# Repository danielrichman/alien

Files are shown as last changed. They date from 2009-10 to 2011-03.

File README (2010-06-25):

This is the code repository for the ALIEN Project:
ALtitude Imaging Entering Near-space

This project consists of
  Daniel Richman <main@danielrichman.co.uk>
  Simrun Basuita <simrunbasuita@googlemail.com>
  Alex Breton 
although Alex Breton will not be contributing any code

More information is here:
  http://wiki.ukhas.org.uk/projects:alien
  http://alienproject.wordpress.com/

All the code contained within this subversion repository is licensed under
GPL version 3. Please see the COPYING file.

All the code is Copyright (c) 2009: Daniel Richman (and/or) Simrun Basuita
Please see individual files for more details.

There are also some schematics licensed under the 
Creative Commons Attribution-Non-Commercial-Share Alike 2.0 UK: 
  England & Wales license.
Typically these are in alien1/eagle and alien2/eagle, and are marked 
accordingly.

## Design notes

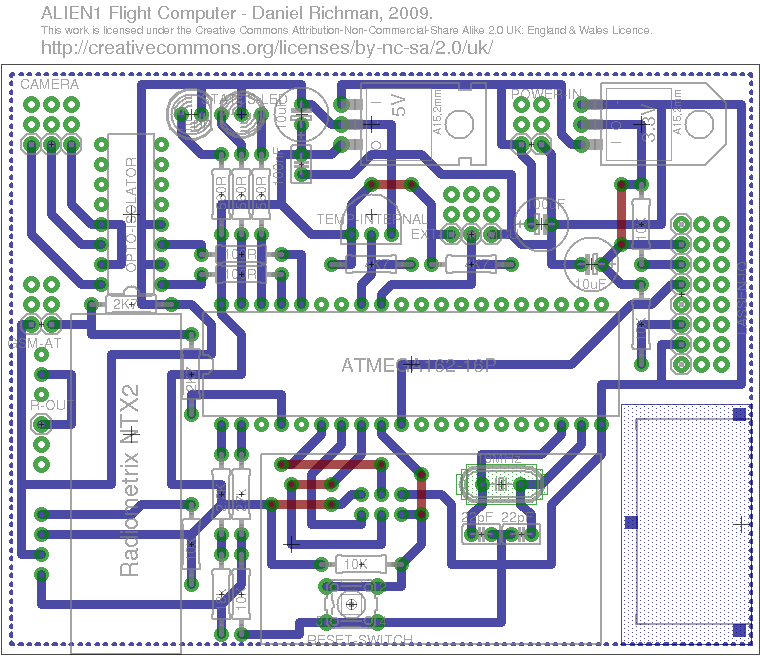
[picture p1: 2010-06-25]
alien1/eagle/alien1b.png

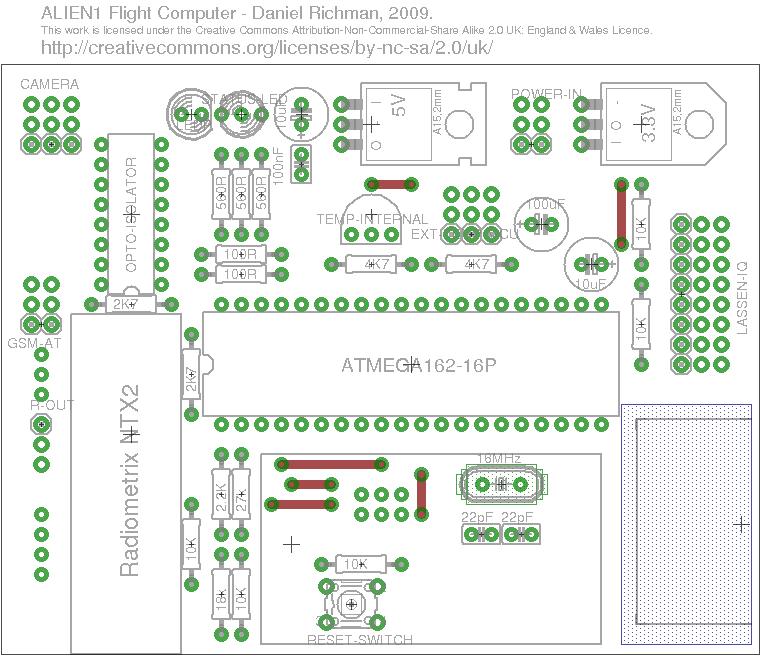
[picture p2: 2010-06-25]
alien1/eagle/alien1bn.png

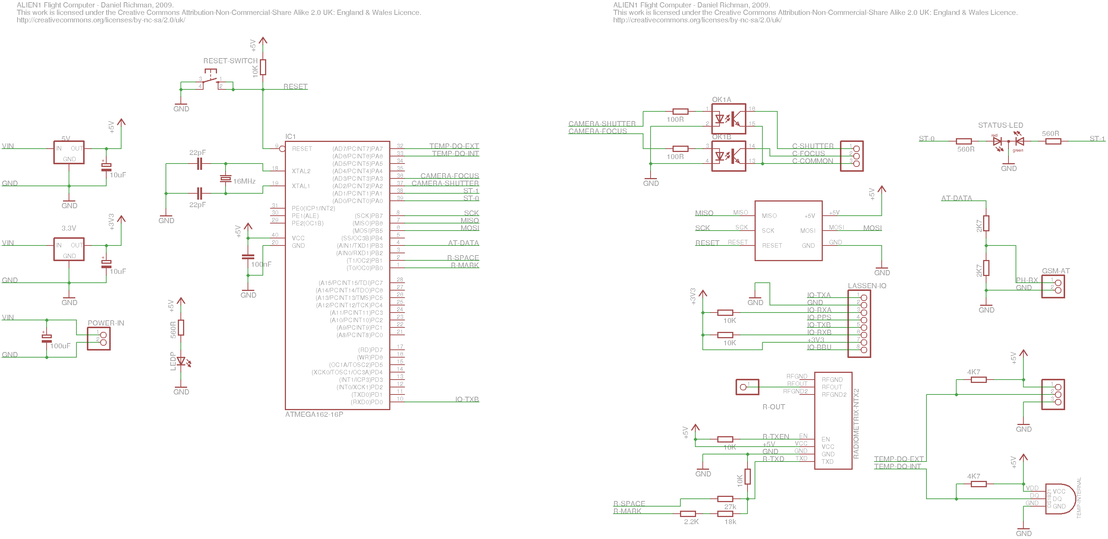
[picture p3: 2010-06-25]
alien1/eagle/alien1.png

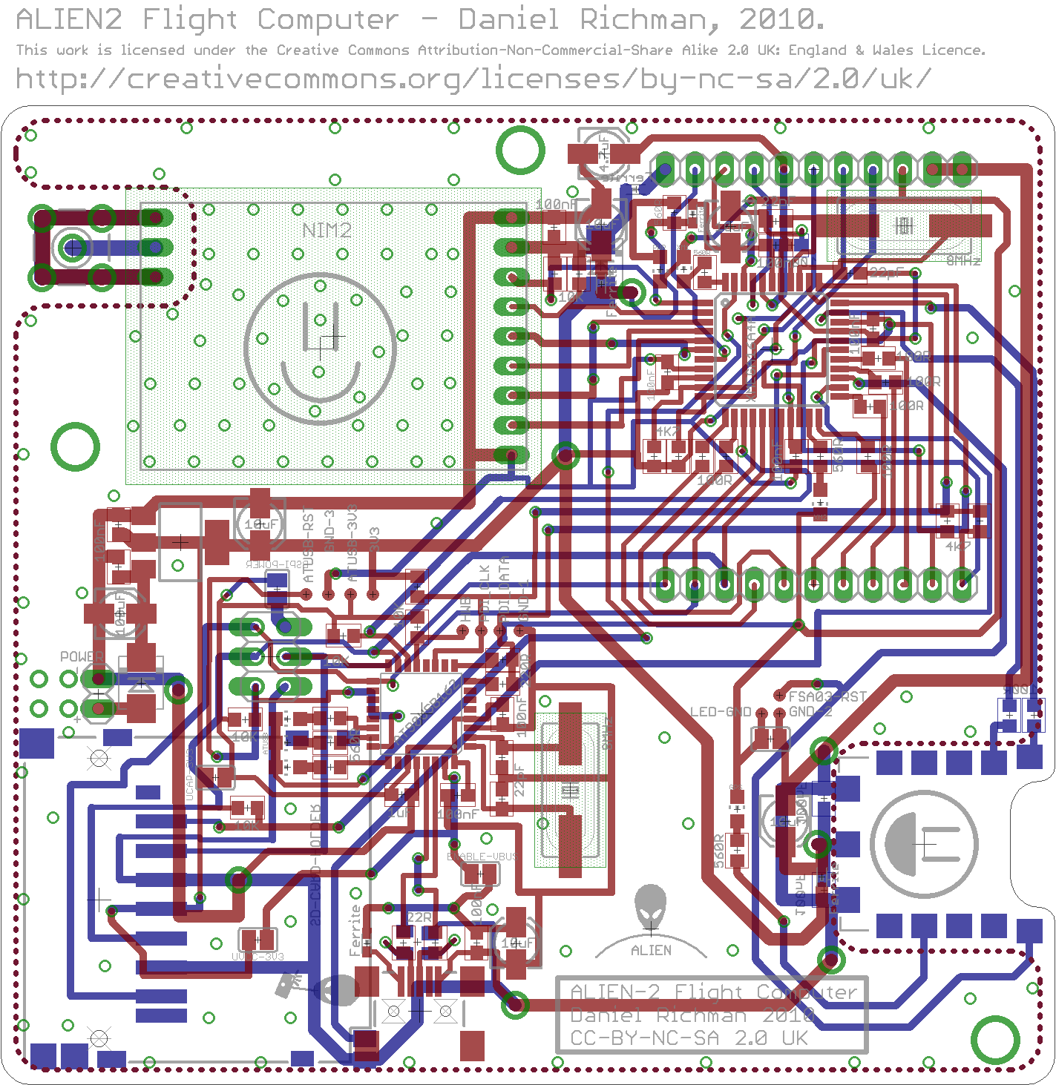
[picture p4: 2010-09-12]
alien2/eagle/alien2b.png

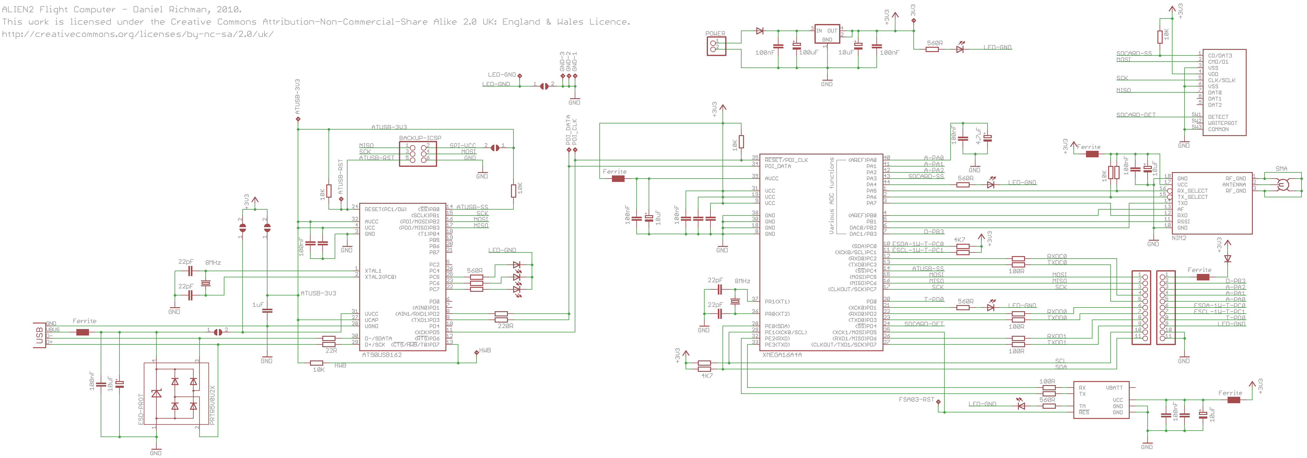
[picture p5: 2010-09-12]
alien2/eagle/alien2.png

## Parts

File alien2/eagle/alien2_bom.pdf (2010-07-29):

| Value | Device
2 | 22R | Resistor 0603 | 1500608
8 | 100R | Resistor 0603 | 1500583
2 | 220R | Resistor 0603 | 1500609
7 | 560R | Resistor 0603 | 1500642
4 | 4K7 | Resistor 0603 | 1500637
7 | 10K | Resistor 0603 | 1500585
4 | 22pF | Capacitor 0603 | 1414622
12 | 100nF | Capacitor 0603 | 1650834
1 | 1uF | Capacitor 0603 | 1650837
1 | 4.7uF | Electrolytic Capacitor 0405 | 1187021
5 | 10uF | Electrolytic Capacitor 0405 | 1469324
1 | 100uF | Electrolytic Capacitor 0603 | 8823065
2 | 8MHz | Crystal | 1611741
1 | | AT90USB162 | 1455073
5 | | Ferrite Bead 0603 | 1515756
3 | | Red LED 0805 | 1226392
2 | | Yellow LED 0805 | 1226420
2 | | Green LED 0805 | 1226373
1 | | PRTR5V0U2X | 1524157
1 | | SD Card Holder | 9186174
2 | | | 1651108
1 | | SMA | 1248989
1 | | TC2117-3.3V | 1605581
1 | | USB Connector | 1753806
1 | | XMEGA32A4 | 1748557
1 | | FSA03 | Already Have
1 | | NIM2 | Already Have
2 | | Pin Header 1x11
1 | | Pin Header 1X2
1 | | Pin Header 2x3
Qty | Farnell Order Code

Shottky Diode

Maplin
Maplin
Maplin

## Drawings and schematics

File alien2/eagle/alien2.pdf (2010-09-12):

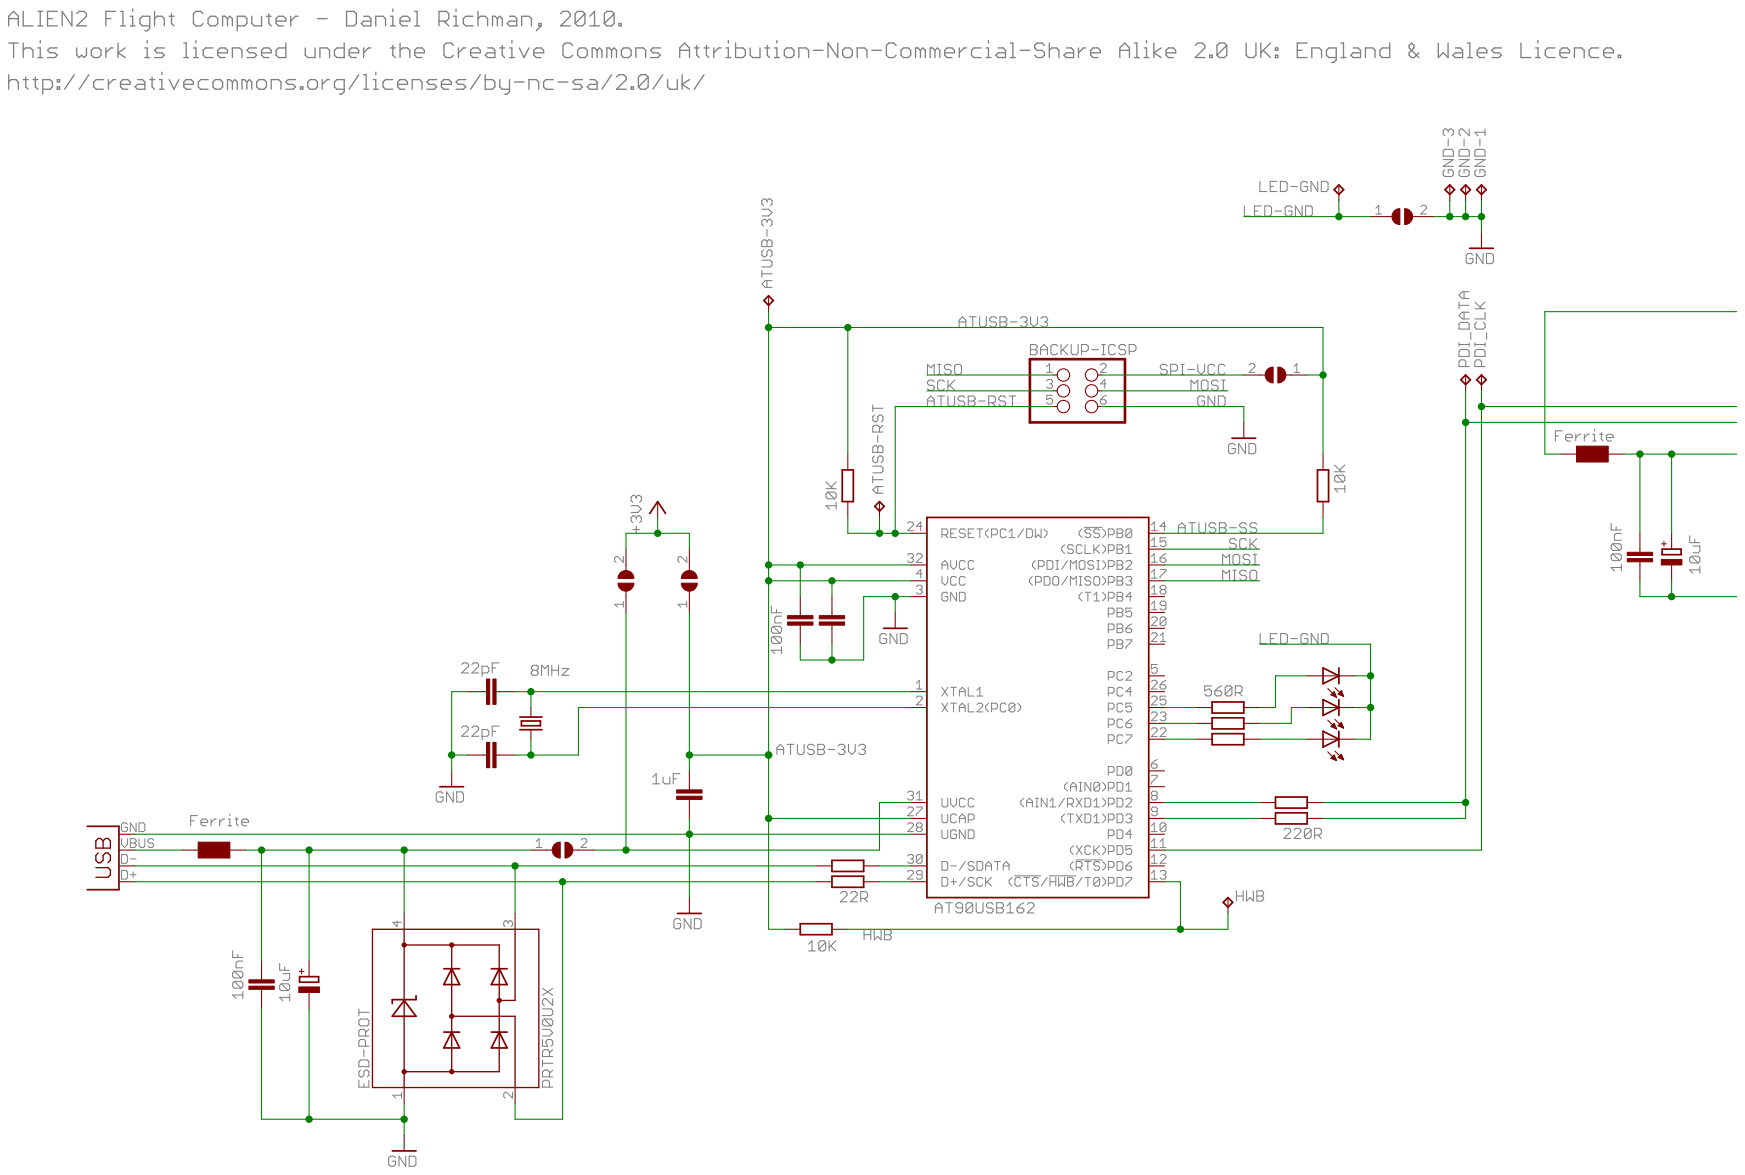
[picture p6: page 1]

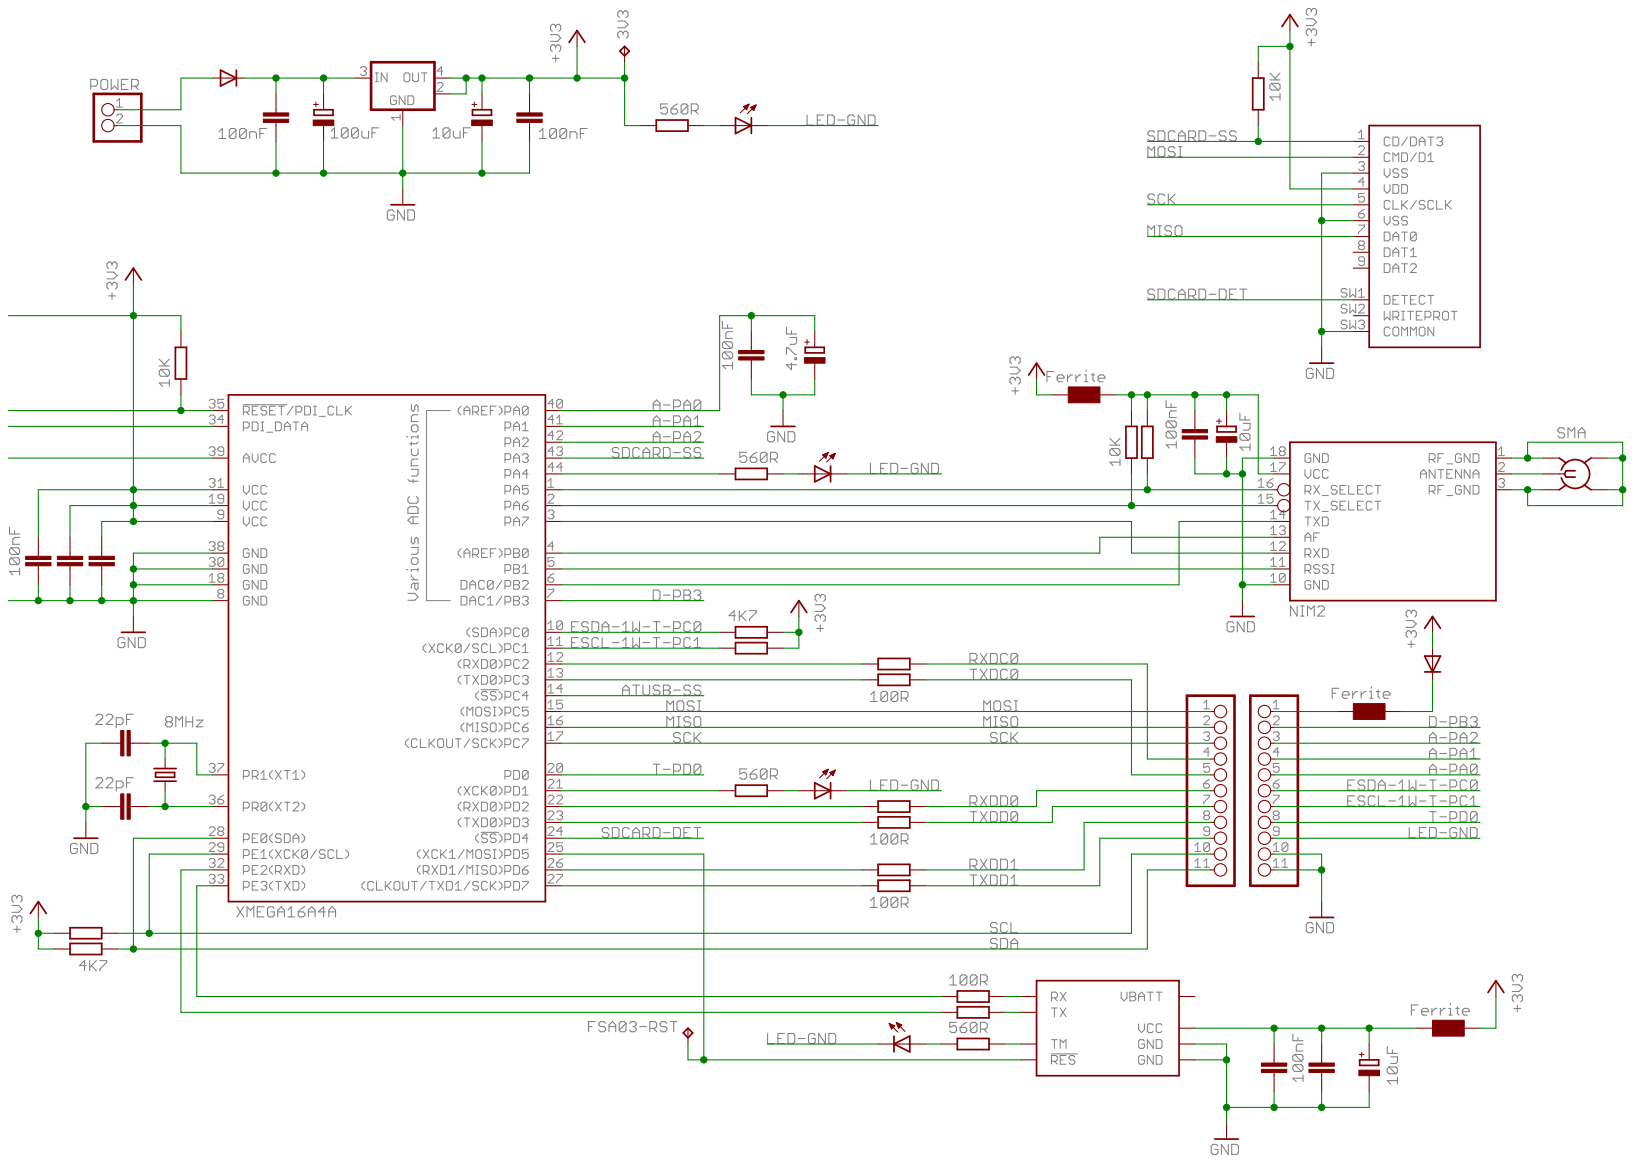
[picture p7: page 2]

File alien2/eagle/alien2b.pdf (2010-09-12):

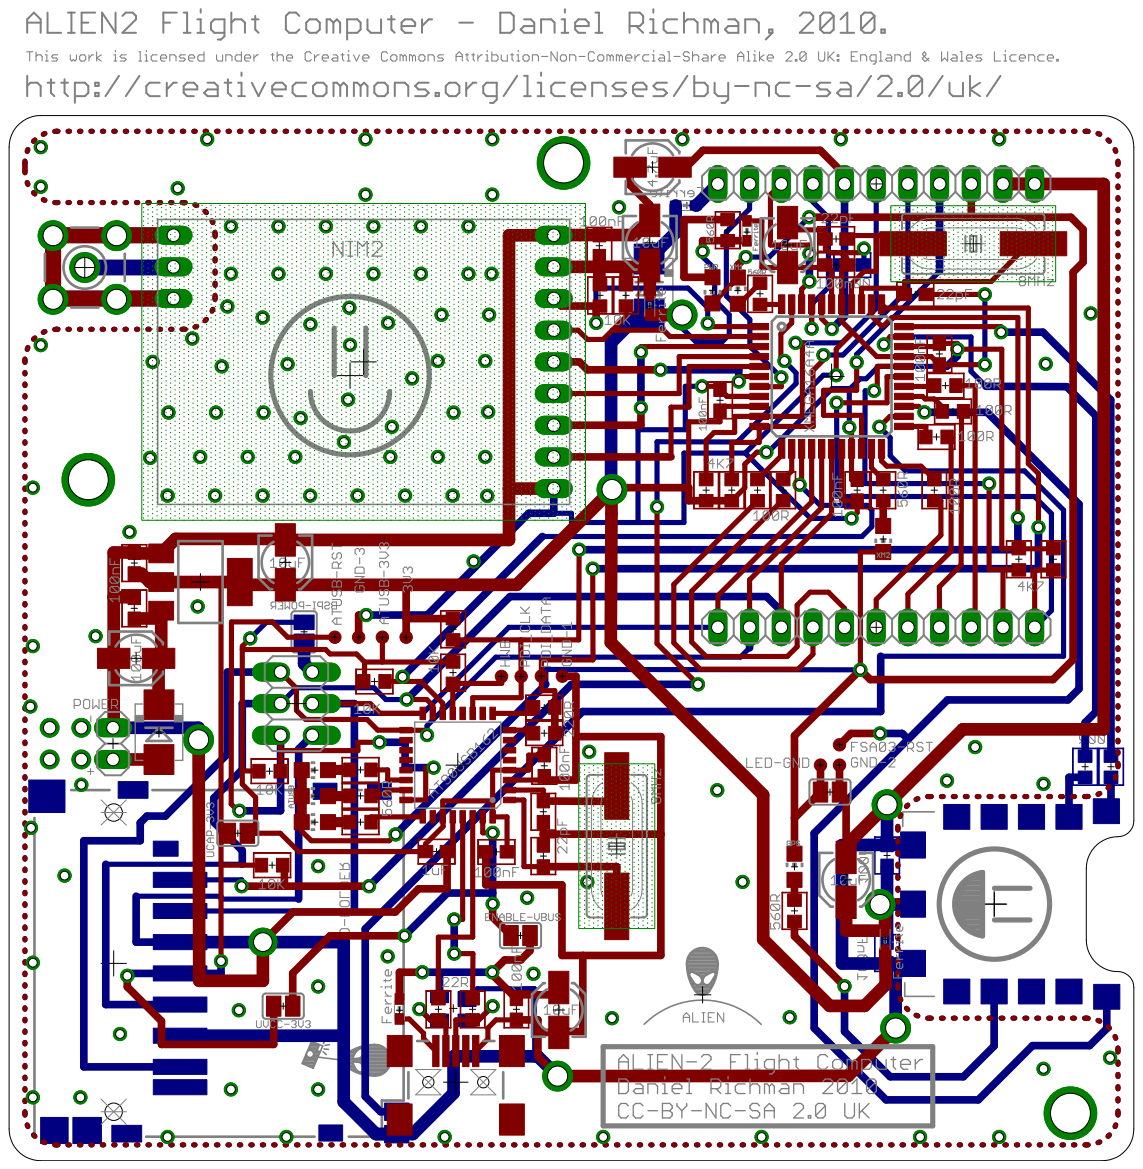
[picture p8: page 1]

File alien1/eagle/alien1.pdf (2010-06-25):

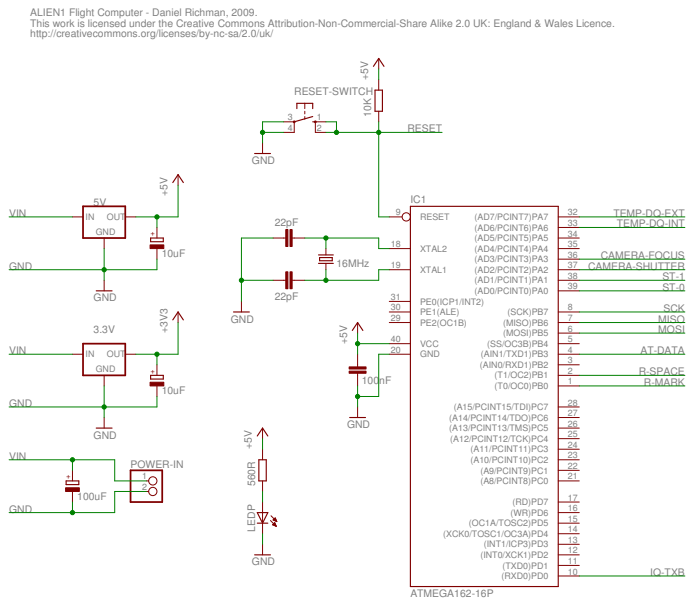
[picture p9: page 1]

ALIEN1 Flight Computer - Daniel Richman, 2009. This work is licensed under the Creative Commons Attribution-Non-Commercial-Share Alike 2.0 UK: England & Wales Licence. http://creativecommons.org/licenses/by-nc-sa/2.0/uk/

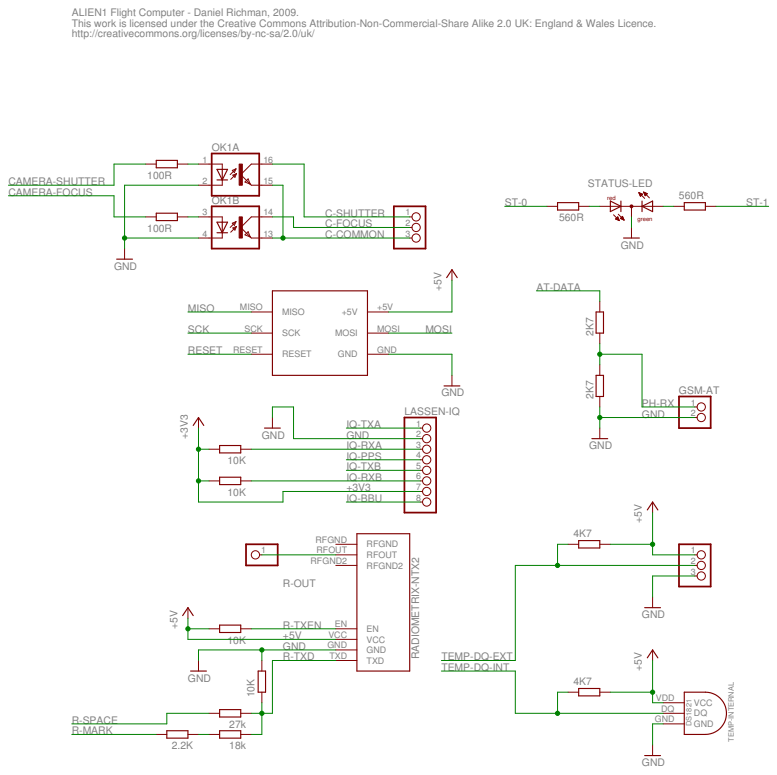
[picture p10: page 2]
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

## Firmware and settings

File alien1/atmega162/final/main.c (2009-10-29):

/*
    Copyright (C) 2008  Daniel Richman

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
    For a full copy of the GNU General Public License, 
    see <http://www.gnu.org/licenses/>.
*/

#include <avr/interrupt.h>
#include <avr/sleep.h>
#include "main.h"
#include "gps.h"
#include "log.h"
#include "radio.h"
#include "sms.h"
#include "statusled.h"
#include "timer1.h"
#include "timer3.h"
#include "watchdog.h"

int main()
{
  gps_init();
  log_init();
  radio_init();
  sms_init();
  statusled_init();
  timer1_init();
  timer3_init();
  watchdog_init();

  /* Interrupts on - go go go! */
  sei();

  /* Now sleep - the whole program is interrupt driven */
  for (;;) sleep_mode();
}

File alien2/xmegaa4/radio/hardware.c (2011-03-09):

/*
    Copyright (C) 2010  Daniel Richman

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
    For a full copy of the GNU General Public License, 
    see <http://www.gnu.org/licenses/>.
*/

#include <stdint.h>
#include <avr/interrupt.h>
#include <avr/io.h>
#include "hardware.h"
#include "radio.h"

#define RADIO_HW_MODE_PORT       PORTA
#define RADIO_DAC                DACB
#define RADIO_ADC                ADCA
#define RADIO_ADC_INPUT_AF       (ADC_CH_MUXPOS_PIN0_gc | ADC_CH_MUXPOS3_bm)
#define RADIO_ADC_INPUT_RSSI     (ADC_CH_MUXPOS_PIN1_gc | ADC_CH_MUXPOS3_bm)
#define RADIO_ADC_CAPT_PREEMPT   10
#define RADIO_HW_TIMER           TCC0
#define RADIO_HW_EVCHMUX         CH0MUX
#define RADIO_HW_EVCHSRC         EVSYS_CHMUX_TCC0_CCA_gc

static void radio_hw_dac_start();
static void radio_hw_dac_stop();
static void radio_hw_adc_init();
static void radio_hw_adc_start();
static void radio_hw_adc_stop();
static void radio_hw_timer_init();

static uint8_t radio_hw_dac_running, radio_hw_adc_running;
static uint8_t radio_hw_adc_cca_decrement;

ISR (TCC0_OVF_vect)
{
    radio_isr();
}

void radio_hw_init()
{
    radio_hw_timer_init();
    radio_hw_adc_init();
}

static void radio_hw_dac_start()
{
    RADIO_DAC.CTRLA = DAC_CH0EN_bm | DAC_ENABLE_bm;
    RADIO_DAC.CTRLC = DAC_REFSEL_INT1V_gc;
    radio_hw_dac_running = 1;
}

static void radio_hw_dac_stop()
{
    RADIO_DAC.CTRLA = 0;
    radio_hw_dac_running = 0;
}

void radio_hw_dac_set(uint16_t value)
{
    RADIO_DAC.CH0DATA = value;
}

static void radio_hw_adc_init()
{
    RADIO_ADC.REFCTRL = ADC_REFSEL_VCC_gc;
    RADIO_ADC.CH0.CTRL = ADC_CH_INPUTMODE_SINGLEENDED_gc;
    RADIO_ADC.CH0.MUXCTRL = RADIO_ADC_INPUT_AF;
    RADIO_ADC.CH1.CTRL = ADC_CH_INPUTMODE_SINGLEENDED_gc;
    RADIO_ADC.CH1.MUXCTRL = RADIO_ADC_INPUT_RSSI;
    RADIO_ADC.EVCTRL = ADC_SWEEP_01_gc | ADC_EVSEL_0123_gc |
                       ADC_EVACT_SWEEP_gc;
    RADIO_ADC.CTRLB = ADC_RESOLUTION_12BIT_gc;
}

static void radio_hw_adc_start()
{
    RADIO_ADC.CTRLA = ADC_ENABLE_bm;
    radio_hw_adc_running = 1;
}

static void radio_hw_adc_stop()
{
    RADIO_ADC.CTRLA = 0;
    radio_hw_adc_running = 0;
}

void radio_hw_adc_get(uint16_t *af, uint16_t *rssi)
{
    *af = RADIO_ADC.CH0.RES;
    *rssi = RADIO_ADC.CH1.RES;
}

static void radio_hw_timer_init()
{
    RADIO_HW_TIMER.INTCTRLA = TC_OVFINTLVL_HI_gc;
    EVSYS.RADIO_HW_EVCHMUX = RADIO_HW_EVCHSRC;
}

void radio_hw_timer_set(uint8_t div, uint16_t per)
{
    /* DIV1 = 1, DIV2 = 2, DIV4 = 3, e.t.c., so this works: */
    radio_hw_adc_cca_decrement = RADIO_ADC_CAPT_PREEMPT >> (div - 1);
    if (radio_hw_adc_cca_decrement == 0)
        radio_hw_adc_cca_decrement = 1;

    RADIO_HW_TIMER.CTRLA = 0;
    RADIO_HW_TIMER.CTRLFSET = TC_CMD_RESTART_gc;
    RADIO_HW_TIMER.PER = per;
    RADIO_HW_TIMER.CCA = per - radio_hw_adc_cca_decrement;
    RADIO_HW_TIMER.CTRLA = div;
}

void radio_hw_queue_period_update(uint16_t per)
{
    RADIO_HW_TIMER.PERBUF = per;
    RADIO_HW_TIMER.CCABUF = per - radio_hw_adc_cca_decrement;
}

/*
 * If we genuinely put the radio into idle then when we turned it back on
 * there would be a *massive* warmup time while it approaches the correct
 * frequency. This is a total pain and totally breaks hell & morse, and
 * produces an annoying warm up time for rtty and domex.
 */
#define IDLE_FREQ 4000

void radio_hw_mode(uint8_t mode)
{
    uint8_t set_idle_freq;
    set_idle_freq = 0;

    if (mode == RADIO_HW_MODE_TXOFF)
    {
        mode = RADIO_HW_MODE_TX;
        set_idle_freq = 1;
    }

    RADIO_HW_MODE_PORT.DIRCLR = RADIO_HW_MODE_BITS;

    if (mode != RADIO_HW_MODE_RX && radio_hw_adc_running)
        radio_hw_adc_stop();

    if (mode != RADIO_HW_MODE_TX && radio_hw_dac_running)
        radio_hw_dac_stop();

    if (mode == RADIO_HW_MODE_RX && !radio_hw_adc_running)
        radio_hw_adc_start();

    if (mode == RADIO_HW_MODE_TX && !radio_hw_dac_running)
        radio_hw_dac_start();

    if (set_idle_freq)
        radio_hw_dac_set(IDLE_FREQ);

    RADIO_HW_MODE_PORT.DIRSET = mode;
}

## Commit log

2009-04-18 * Added a note on using STTY to set the baudrate * Added tests/ folder and final/ folder to alien1/arduino-168/ * Added a test avr-c program that generates a 50hz interrupt * Added uart-passthrough.c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
    -- Daniel Richman Sat, 18 Apr 2009 22:42:24 +0100
2009-04-18 * Copied misc-c/gps-example.c to alien1/arduino-168/final/gps.c and slightly AVR-ified it. Needs to be completed and tested ;) * Created alien1/arduino-168/final/radio.c with a first implementation o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
    -- Daniel Richman Sun, 19 Apr 2009 00:34:26 +0100
2009-04-19 * Made alien1/arduino-168/final into a proper multi-object program * Added headers * Reorganised a few structs into messages.h * Fixed bugs * Consolidated _init() functions and added main.c * Adadpte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
    -- Daniel Richman Sun, 19 Apr 2009 13:39:57 +0100
    [main.c, radio.c]
2009-04-19 * Added UART support to gps.c * Added timer1.c to generate 50hz, 1hz and 1/60hz procs, 50hz for radio, 1hz for general routine, and 60hz for temperature sensor trigger * Added temperature.c and tempe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
    -- Daniel Richman Sun, 19 Apr 2009 20:13:55 +0100
    [main.c, radio.c, temperature.c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]
2009-04-21 * *.c: Fixed up the header #includes * *.h: Changed ALIEN1_* to ALIEN_ and added #include <stdint.h> where the header requires it * timer1.c: Added timer1_uart_idle_counter to help the future sms.c w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
    [main.c, radio.c]
2009-04-21 * Added analyse_memory script that prints data and statistics on the AVR program, and how much RAM, Program Memory, .data .bss and .text is used * Added analyse-memory target to Makefile that creates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
    -- Daniel Richman Tue, 21 Apr 2009 21:01:13 +0100
2009-04-22 * Makefile: upgraded avr_size call to print more info on which object is using the space, and moved avr_gcc binaries to variable names for easier changing * messages.c: Finished messages_get_char * m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
    -- Daniel Richman Wed, 22 Apr 2009 19:56:52 +0100
2009-04-22 * Added temperature_age * Fixed timer1.c gpio note * Started temperature.c work, changed prototypes slightly
    -- Daniel Richman Wed, 22 Apr 2009 22:16:49 +0100
    [temperature.c, temperature.h, timer1.c]
2009-04-23 * timer1.c and temperature.c - fixed broken Timer settings * temperature.c - more work on temperature sensing * messages.c - added message_id incrementor
    -- Daniel Richman Thu, 23 Apr 2009 22:33:30 +0100
    [temperature.c, temperature.h, timer1.c]
2009-04-24 * created arduino-168/tests/temptest.c to test final/temperature.c * updated tests/Makefile to make avr-size call better * created empty camera.c and camera.h * final/*.c: added camera.h * timer1.c: 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
    -- Daniel Richman Sat, 25 Apr 2009 00:54:23 +0100
    [radio.c, temperature.c, temperature.h]
2009-04-25 * Fixed the byte that ubits were modifying in temperature.h * Flipped byte order to print debug info in big-endian rather than the little endian on the AVR * Fixed temperature_state looping when only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
    -- Daniel Richman Sat, 25 Apr 2009 01:44:19 +0100
    [temperature.c, temperature.h]
2009-04-25 * Fixed a couple of bugs in final/messages.c - added a catch for the power-on gps data-nulls, replace with '!'; fixed a bug where there was no comma field separator on the message_id * Changed all us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
    -- Daniel Richman Sat, 25 Apr 2009 09:38:36 +0100
    [main.c, radio.c, temperature.c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]
2009-04-25 * Added radiotest.c that just sends one string over the radio constantly * Added messagetest.c that tests the message_get_char function by echoing data to the UART
    -- Daniel Richman Sat, 25 Apr 2009 09:39:43 +0100
2009-04-26 * Added radiovolttest.c to test the voltages of the radio by sending marks/spaces at 1hz * Modified radio.c to use two GPIOs instead of 1 * Updated ALIEN message format in messages.c
2009-04-27 * Added debugging code to gps.c, enabled by a #define * Created gpstest.c * Fixed bugs in gps.c to bring it up to a fully working state
    -- Daniel Richman Mon, 27 Apr 2009 21:11:08 +0100
    [gpstest.c]
2009-04-28 * radio.c: Removed RADIO_MARK and RADIO_SPACE functions and replaced with a stack variable to save space & improve niceness. Also added _substate for readability, and speed * radio.c: Added half seco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
    -- Daniel Richman Tue, 28 Apr 2009 18:32:19 +0100
    [radio.c, timer1.c]
2009-04-29 * gpstest.c: fixed it to work with the new sms.c * timer1.c: added sms_state_wait code * sms.c: completed & tested - success! * messages.c: added satellite count * messages.c: changed message_header_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
    -- Daniel Richman Wed, 29 Apr 2009 18:05:31 +0100
    [gpstest.c, timer1.c]
2009-04-29 * Removed useless payload_state_data, and since the message_type was therefore no longer required, removed that too * Updated message formats & sms.c message length
    -- Daniel Richman Wed, 29 Apr 2009 19:50:28 +0100
    [gpstest.c, radio.c, timer1.c]
2009-04-30 * camera.c, camera.h: implemented camera controlling logic * main.c, timer1.c: added camera_ calls
    -- Daniel Richman Thu, 30 Apr 2009 19:54:06 +0100
2009-05-01 * messages.c, log.c, log.h: added logging prototypes & empty functions
    -- Daniel Richman Fri, 01 May 2009 22:07:31 +0100
2009-05-29 * Added sms static test (always sends Hello ALIENs) * Fixed gpstest.c and messagestest.c - added empty logging functions
    [gpstest.c]
2009-05-30 * SVN has problems moving folders so I have to do this commit in a couple of steps. Bigger commit to come!
    -- Daniel Richman Sat, 30 May 2009 20:34:35 +0100
    [gpstest.c, log.c, main.c]
2009-05-31 * Updated sms routines now that it no longer competes with the gps for the UART (although it still competes for processing time)
    -- Daniel Richman Sun, 31 May 2009 11:38:13 +0100
    [main.c, timer1.c]
2009-05-31 * Intermediate commit to move timer1 files around (FTBFS)
    -- Daniel Richman Sun, 31 May 2009 11:40:05 +0100
2009-05-31 * Complete namechange of timer1 to timers
    -- Daniel Richman Sun, 31 May 2009 11:49:49 +0100
2009-05-31 * Upgraded timers.c to use timer3 for the long 1 second waits that sms.c and temperature.c require * As a result many other files had to be upgraded to use this new system
    -- Daniel Richman Sun, 31 May 2009 12:43:34 +0100
2009-05-31 * Call me indecisive, but I've decided to split timers.c to timer1.c and timer3.c ;) * Intermediate commit...
    -- Daniel Richman Sun, 31 May 2009 13:24:50 +0100
2009-05-31 * Completed split of timers.c to timer1.c and timer3.c * Note the difference between the way timer1.c and timer3.c are used: timer1.c is more of a 'parent' organiser, calling the functions of the mod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
    -- Daniel Richman Sun, 31 May 2009 13:40:46 +0100
2009-05-31 * Fixed bugs, added a WDT support, added STATUS LED support * Tweaked functionality of temperature.c to make it work better - changed the way the age ubit works
    -- Daniel Richman Sun, 31 May 2009 18:12:31 +0100
    [gpstest.c, log.c, main.c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]
2009-06-10 * Fixed bad Makefile headers * Fixed watchdog timer initialisation * Added gps_rx_ok counter * Added statusled logic for gps_rx_ok * BTW: It works!
    -- Daniel Richman Wed, 10 Jun 2009 22:17:04 +0100
    [statusled.c, timer1.c]
2009-06-11 * Fixed typos in statusled.c * Removed useless WDT reset signal flashing as it will only flash once * Instead added inital-startup-flash code
    -- Daniel Richman Thu, 11 Jun 2009 18:00:00 +0100
    [statusled.c, timer1.c]
2009-06-19 * Fixed/Updated radio and temperature tests * Fixed tests Makefile * Tightened statusled's fix_age requirement * Increased the hold_lengths for the camera * Toggle notes added to temperature.c * Tidi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
    -- Daniel Richman <daniel@richmanwebsite.co.uk> Fri, 19 Jun 2009 18:24:10 +0100
    [statusled.c, temperature.c]
2009-07-12 * Added (unused) crc7 implementation * Added initial play-with-sd-card arduino test program * Added something to generate some sectors for the card to help debugging * Fixed tests & messages to accep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
    -- Daniel Richman Sun, 12 Jul 2009 21:45:18 +0100
    [gpstest.c, log.c]
2009-07-21 * Tidy up and restructure of folders, corrected ./TREE * Fixed any long-line-length files * Added logtest.c (done no work on it yet)
    -- Daniel Richman Tue, 21 Jul 2009 12:10:21 +0100
    [gpstest.c, sdtest.c]
2009-07-27 * IT WORKS! * (Fixed all the log/sd card files)
    -- Daniel Richman Mon, 27 Jul 2009 01:37:02 +0100
    [log.c]
2009-07-27 * Add dirty hack-script for testing logging on the Arduino
    -- Daniel Richman Mon, 27 Jul 2009 17:08:42 +0100
2009-07-30 * SD CARD CODE WORKS! (really) * Changed it from a 128 message-per-block model to a more appropriate 512 block continuous stream of messages model since 128 byte blocks didn't appear to work. * Tweak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
    -- Daniel Richman Thu, 30 Jul 2009 16:25:31 +0100
    [gpstest.c, log.c, sdtest.c]
2009-08-09 * Removed all uses of _BV * Cleaned up #includes so that only required ones are used * Moved gps_rx_ok to latest_data.system_state, adding MCUCSR * Moved system_location.fix_age to system_fix_age * M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
    -- Daniel Richman Mon, 10 Aug 2009 00:35:32 +0100
    [log.c, main.c, radio.c]
2009-08-09 * Upgraded temperature_ubits_toggle_a/b to a better, 5 bit rolling counter (see temperature.c/h)
    -- Daniel Richman Mon, 10 Aug 2009 00:50:58 +0100
2009-08-10 * Fixed log.c: slight restructuring to accomodate for messages.c * Updated tests to reflect this * Added log_ok to system_state, removed all MCUCSR bits except for WDT
    -- Daniel Richman Mon, 10 Aug 2009 23:37:21 +0100
    [gpstest.c, log.c, statusled.c]
2009-08-10 * Fix typo in temperature.c toggle logic
    -- Daniel Richman Mon, 10 Aug 2009 23:47:51 +0100
    [temperature.c]
2009-08-11 * Made timer1.c trigger temperature.c & sms.c at poweron aswell as every 1 and 5 minutes respectivly.
    -- Daniel Richman Tue, 11 Aug 2009 19:34:32 +0100
2009-08-11 * Given temperature precedence over sms in timer1.c's scheduling (they compete for use of timer3
    -- Daniel Richman Tue, 11 Aug 2009 20:45:20 +0100
2009-08-16 * Tweaks to sms.c and messages.c to fix $ characters * Tweaks to log.c to use more of the available card space * Fixed logtest.c
    -- Daniel Richman Sun, 16 Aug 2009 18:13:13 +0100
    [log.c]
2009-09-18 * Fixed sms triggering code * Adjusted radio pause length
    -- Daniel Richman Fri, 18 Sep 2009 18:24:17 +0100
    [radio.c, timer1.c]
2009-10-29 * Removed camera code since we're now controlling the camera separatly
    -- Daniel Richman Thu, 29 Oct 2009 14:43:40 +0000
2010-06-25 Added eagle files
    [alien1.brd, alien1.sch, alien2.sch]
2010-06-25 Added ALIEN-2 eagle BOM
    [alien2_bom.csv]
2010-06-25 ALIEN-2: Tweaked sch, added PDF rendering of schematic & its BOM
    [alien2.sch]
2010-06-25 CC (by-nc-sa) licensed schematics, added PNGs for schematics.
    [alien1.brd, alien1.sch, alien2.sch]
2010-06-28 Work on the alien2 pcb layout
    [alien2.brd, alien2.sch]
2010-07-29 Finished ALIEN 2 Board & added gerbers and images of board
    [alien2.brd, alien2.sch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]
2010-07-31 Put resistor squares on PCB
    [alien2.GBO, alien2.GTO]
2010-07-31 Tweaks to the board
    [alien2.brd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]
2010-09-12 Cosmetic changes to board: use vector font & remove silly name
    [alien2.brd, alien2.sch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]
2010-11-24 Added AT SMS code ported to the arduino
2011-03-07 Added ADC support
2011-03-09 Improved sample preempting, sped up debug, added uplink dump, added adc_get

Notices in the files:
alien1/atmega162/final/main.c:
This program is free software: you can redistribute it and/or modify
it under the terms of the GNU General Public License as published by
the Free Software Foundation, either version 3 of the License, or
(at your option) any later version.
